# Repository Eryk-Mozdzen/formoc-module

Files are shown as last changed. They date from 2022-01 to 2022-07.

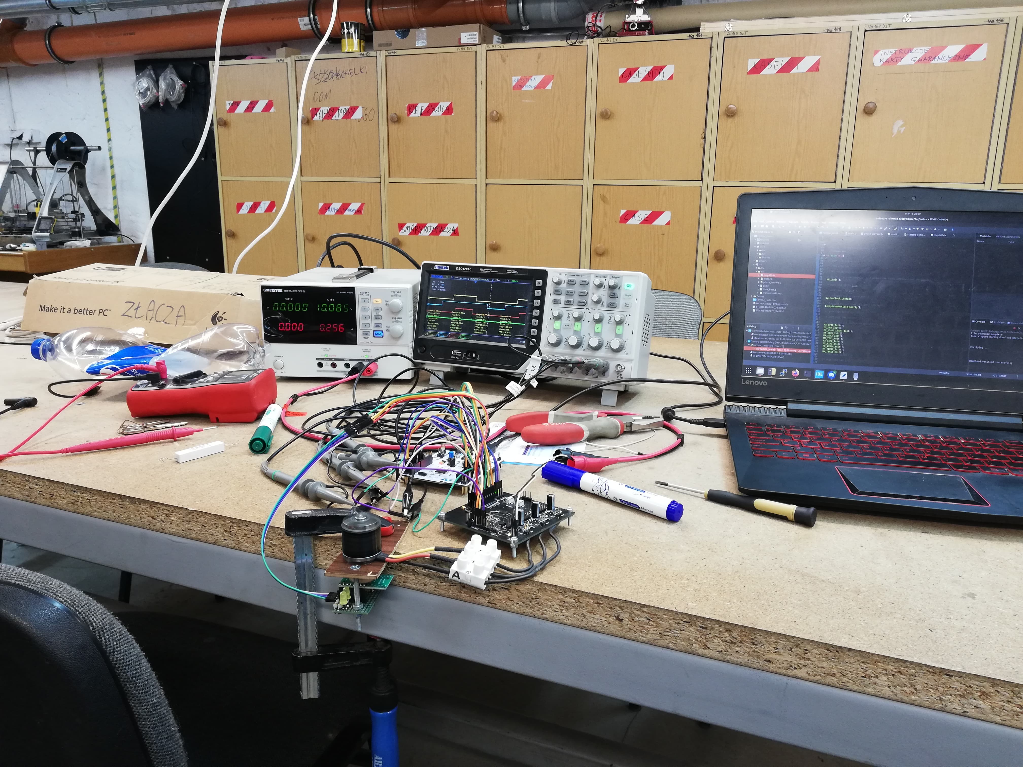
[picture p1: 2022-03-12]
docs/other_photos/275427429_1309768459516400_6027469848381933831_n.jpg

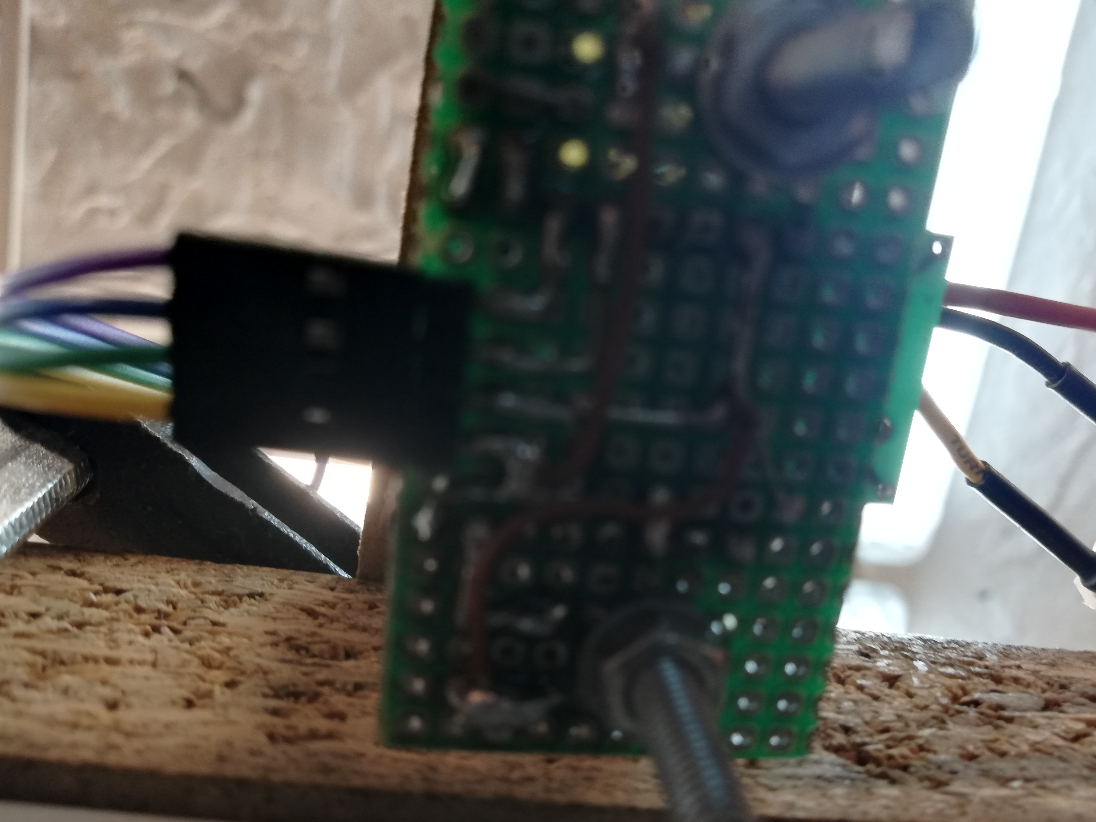
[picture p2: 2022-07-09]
docs/other_photos/IMG_20220304_194742.jpg

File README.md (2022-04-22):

# Field Oriented Motor Controller | FORMOC module
BLDC motor controller using FOC algorithm by Wojciech Bohdan and Eryk Możdżeń.

## Project overview
The goal is to create an opportunity for easy implementation of BLDC motors to small autonomous robots like linefollower or minisumo.

Right now project is in mid development stage.

## Interface

```c
struct {
  uint8_t fdc : 5;  // field code
  uint8_t tg  : 1;  // toggle
  uint8_t rw  : 1;  // read/write operation
  uint8_t mot : 1;  // left/right motor
} msg_header_tx;

struct {
  uint8_t fdc : 5;  // field code
  uint8_t tg  : 1;  // toggle
  uint8_t un  : 1;  // unused
  uint8_t mot : 1;  // left/right motor
} msg_header_rx;

struct {
  uint8_t sta : 7;  // status field
  uint8_t tg  : 1;  // toggle
} msg_hearbeat;
```

| Field | Code  | R/W | Type | Unit | Details |
| ----- | ----  | --- | ---- | ---- | --- |
| status | 0x00  | r/w | `uint8_t` | | bit 0 - MCP8024 error flag <br>bit 1 - read/write access error flag <br> bit 2 - read/write wrong toggle flag <br>  bit 3 - write timeout flag <br> bit 4 - write wrong param flag <br> bit 5-6 (unused) <br> bit 7 (reserved) |
| control (toggle free) | 0x01  | w | `uint8_t` | | bit 0 - reset <br> bit 1-7 (unused) |
|||||||
| hardware config | 0x0A  | r/w | `uint8_t` <br> `uint16_t` <br> `uint16_t` | <br> count <br> count | motor pole pairs <br> encoder CPR <br> encoder offset  |
| Id controller config | 0x0B  | r/w | `float32_t` <br> `float32_t` <br> `float32_t` ||  Kp <br> Ki <br> Kd |
| Iq controller config | 0x0C  | r/w | `float32_t` <br> `float32_t` <br> `float32_t` ||  Kp <br> Ki <br> Kd |
| velocity controller config | 0x0D  | r/w | `float32_t` <br> `float32_t` <br> `float32_t` ||  Kp <br> Ki <br> Kd |
|||||||
| velocity setpoint | 0x11 | w | `float32_t` | rps | |
|||||||
| rotor position | 0x20 | r | `int32_t` | count |
| rotor velocity | 0x21 | r | `float32_t` | rps | |
| power supply voltage  | 0x23 | r | `uint16_t` | mV | |
|||||||
| torque limit | 0x30 | w | `float32_t` | Nm | |
| velocity limit | 0x31 | w | `float32_t` | rps | |

# TODO
- check voltages
- solder cables
- one-way, reliable communication
- GET RID OF OVERCURRENT "PROTECTION"
- improve PID tunning
- find torque measurement method
- improve code organization
- add interface

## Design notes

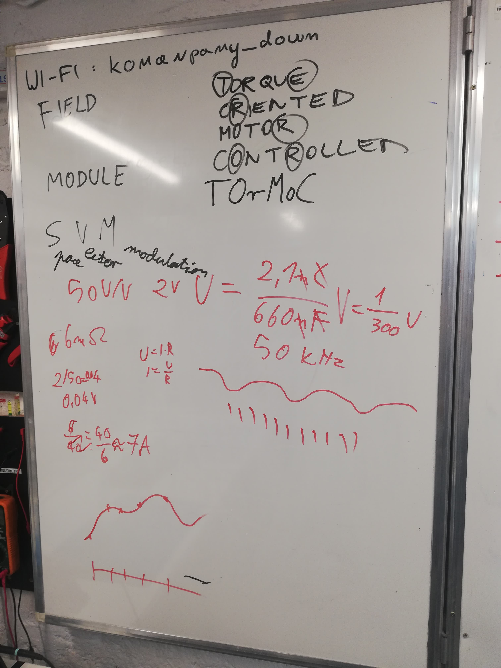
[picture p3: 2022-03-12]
docs/whiteboard_photos/275466424_334416281970746_8824751526483941625_n.jpg

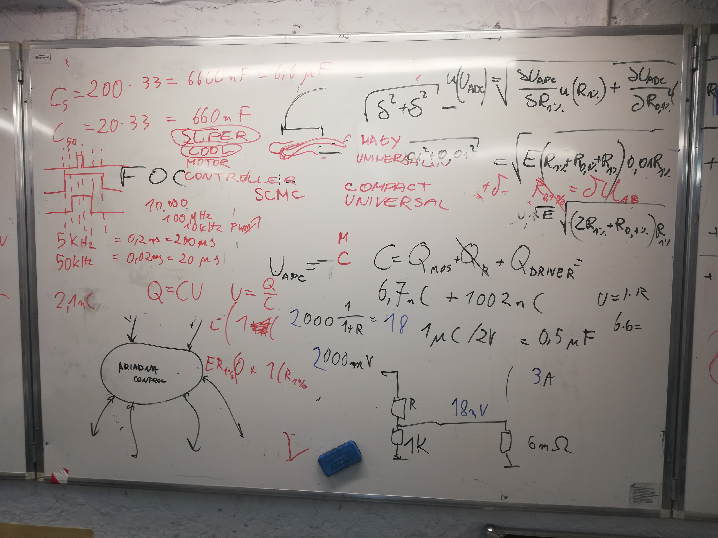
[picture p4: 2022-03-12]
docs/whiteboard_photos/275711006_301435245254634_2206148657679559166_n.jpg

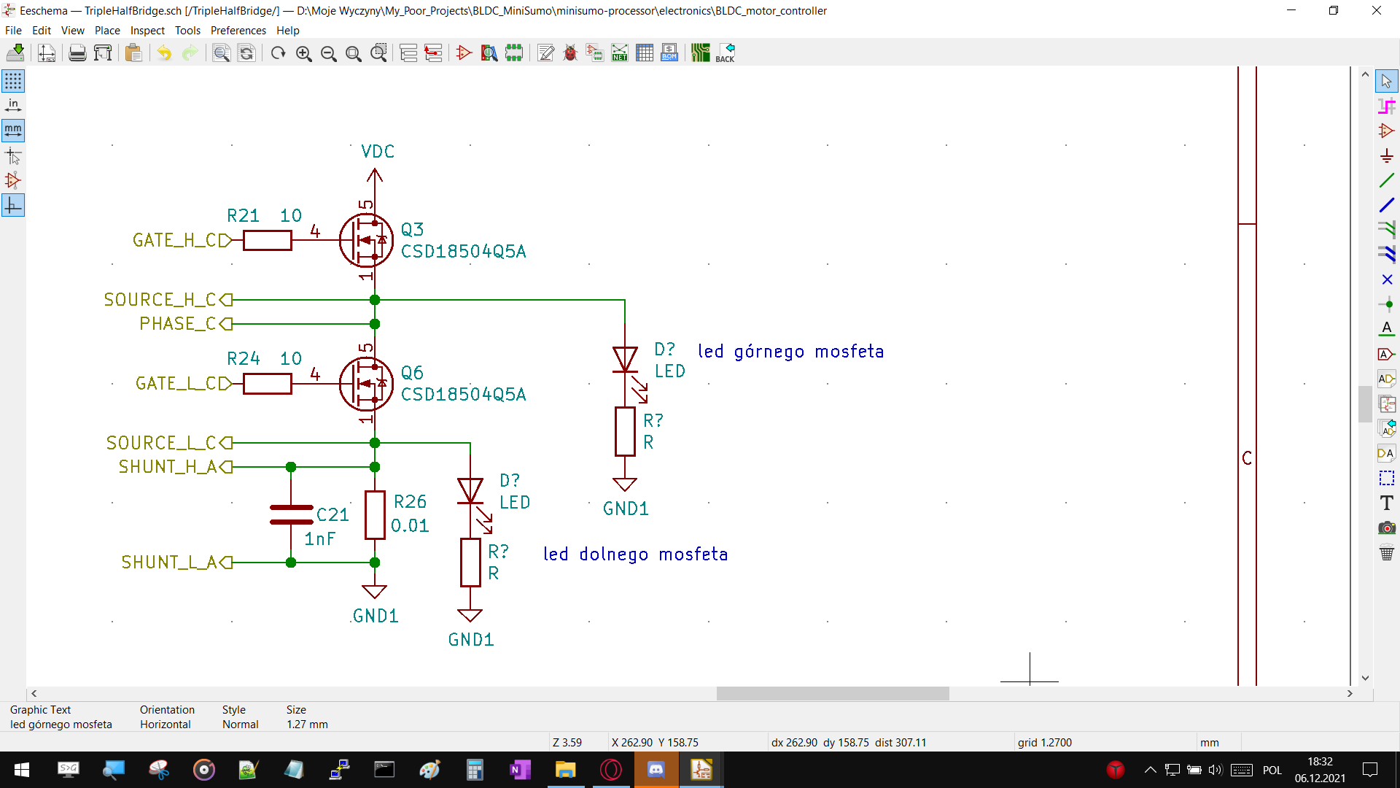
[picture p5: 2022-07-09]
docs/calculations/Screenshot (314).png

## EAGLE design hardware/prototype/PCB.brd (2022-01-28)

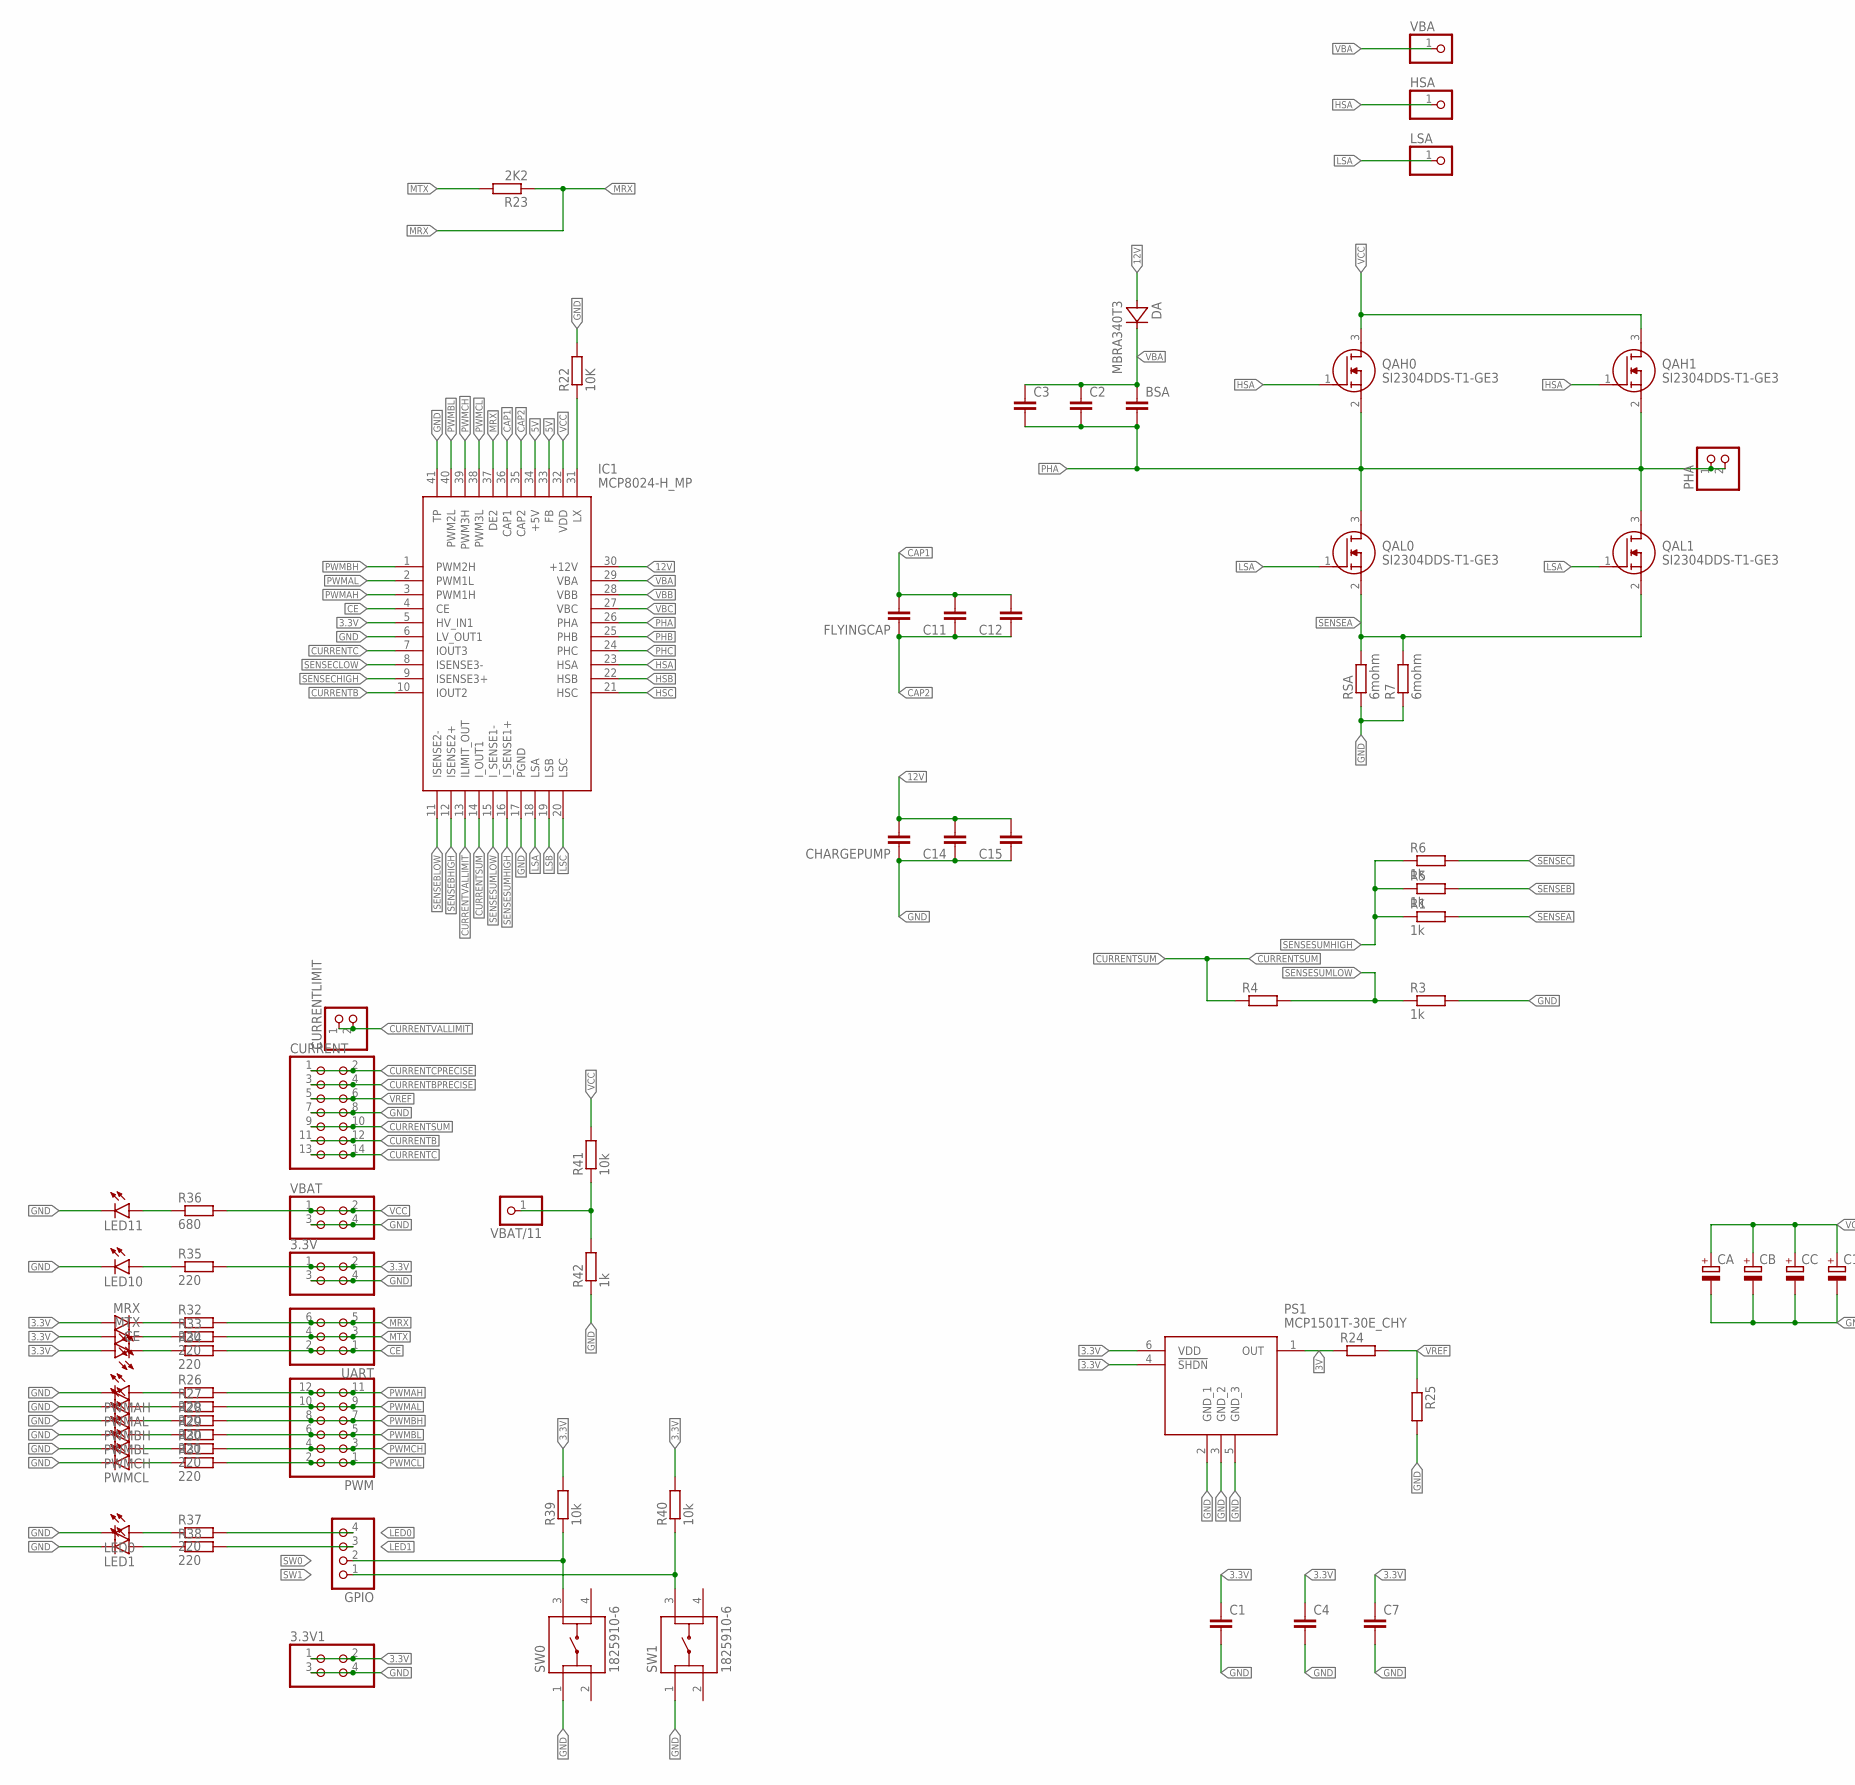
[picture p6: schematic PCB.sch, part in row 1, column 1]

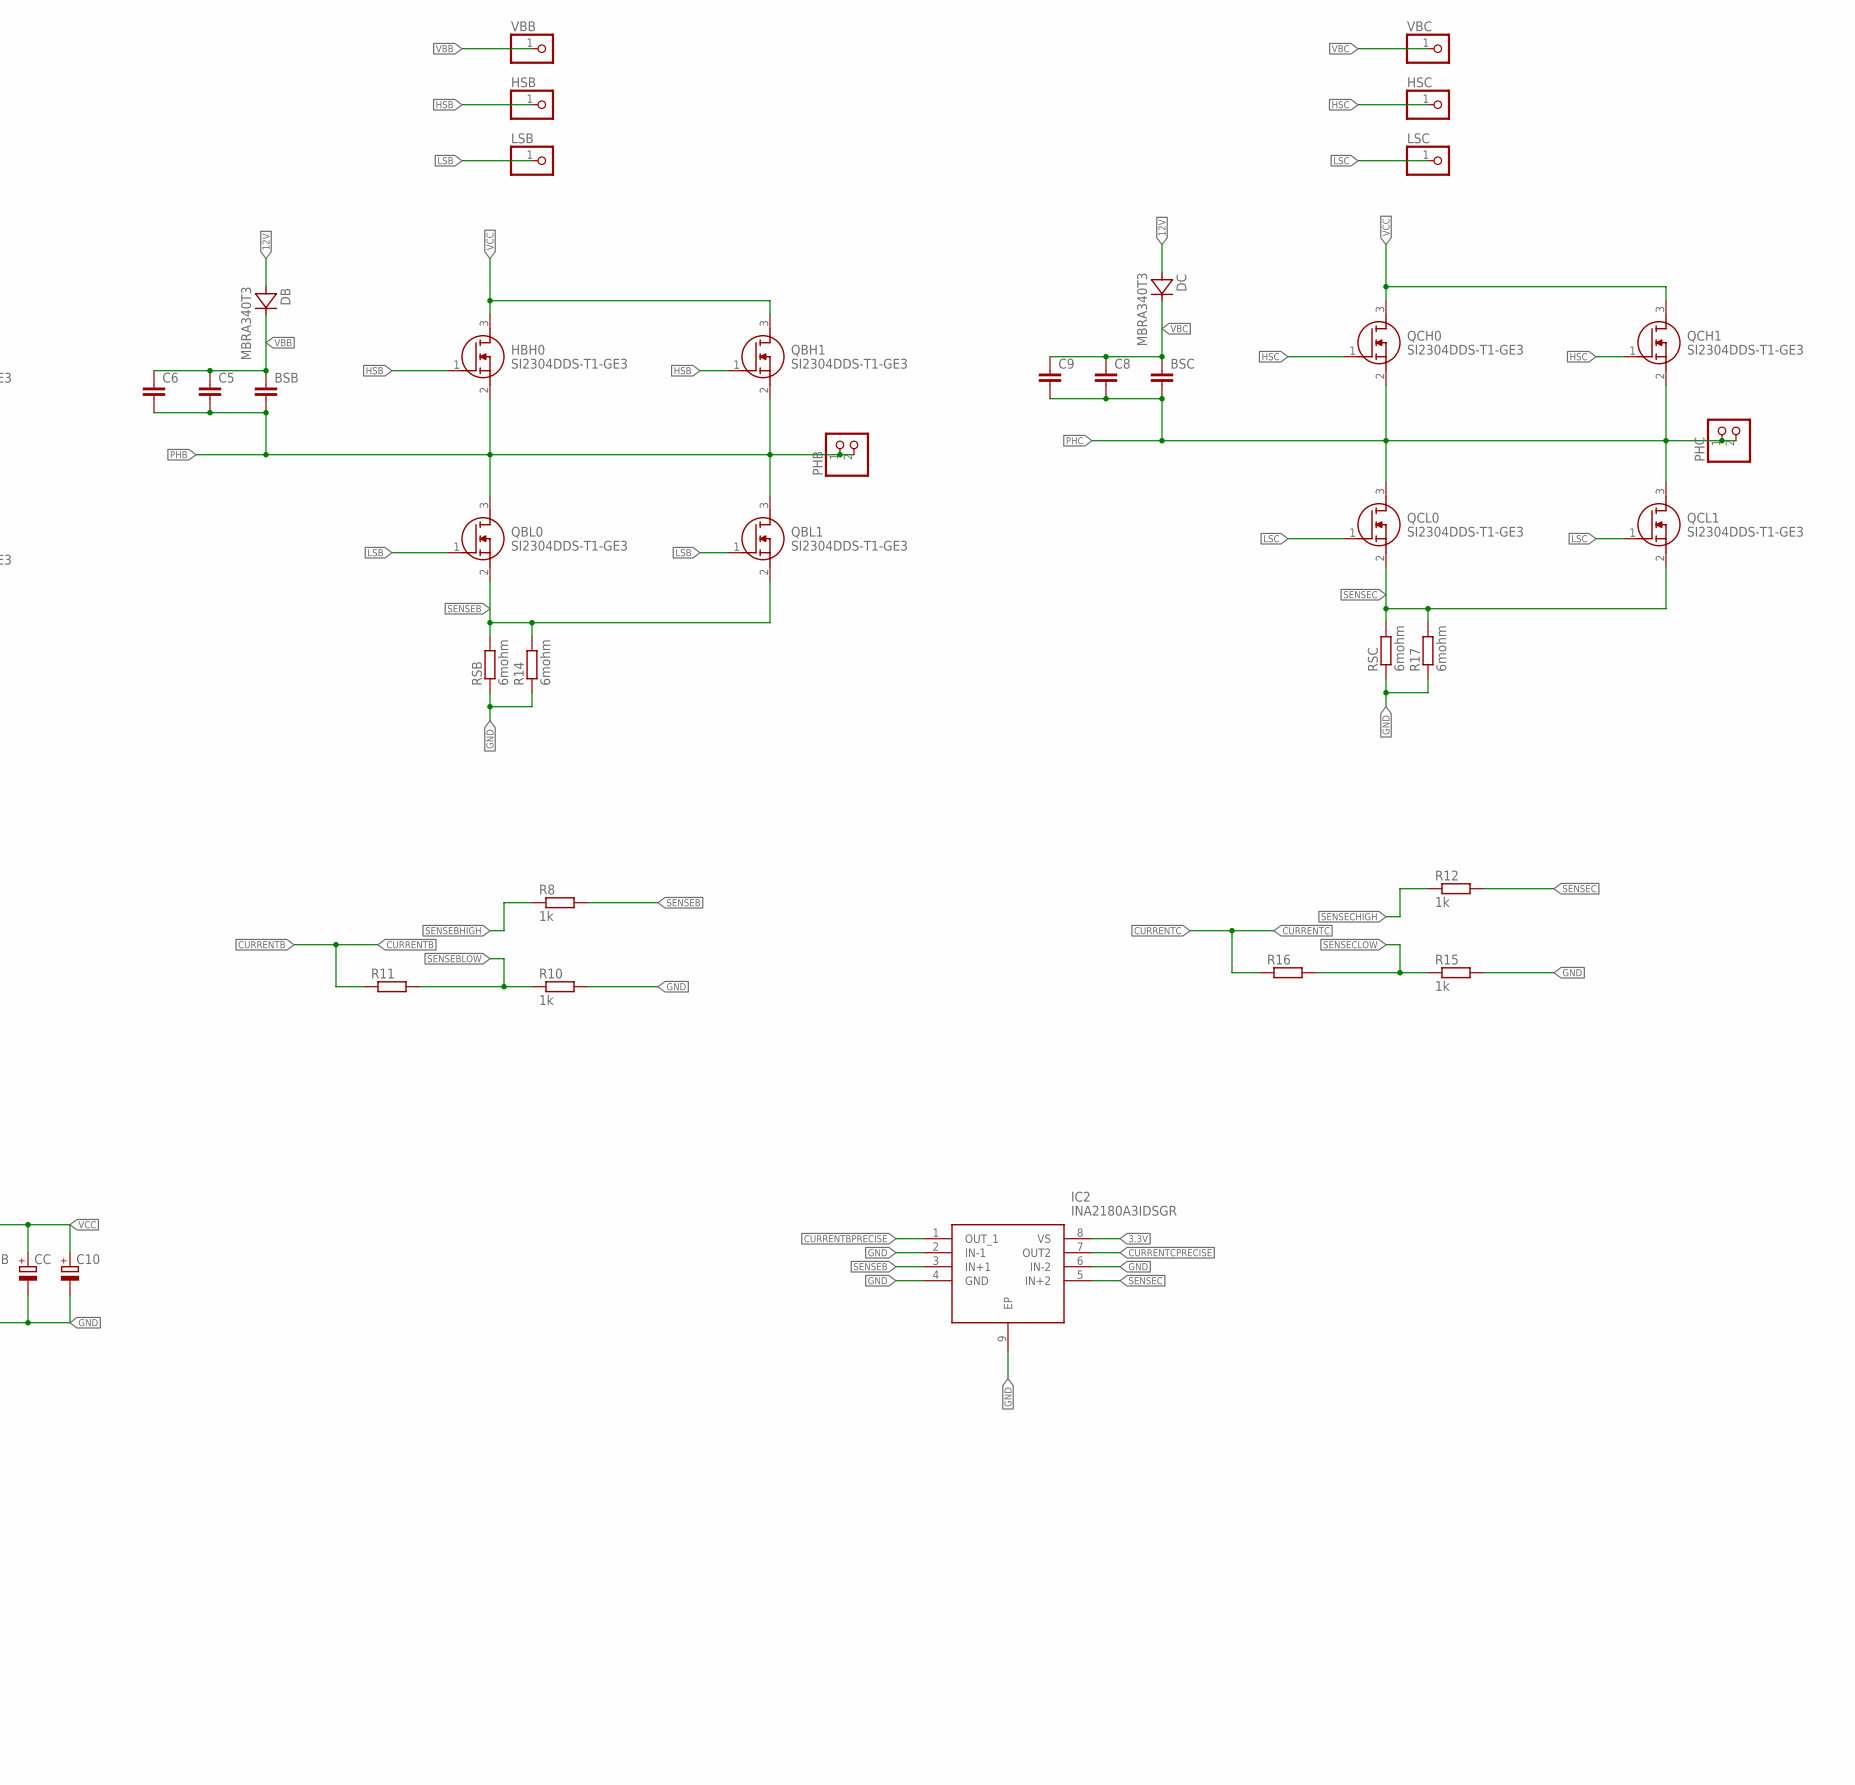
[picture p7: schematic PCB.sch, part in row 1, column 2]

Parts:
3.3V, 3.3V1: PINHD-2X2; 2X02
BSA: C-EUC0603; C0603
BSB: C-EUC0603; C0603
BSC: C-EUC0603; C0603
C1, C2, C3, C4, C5, C6, C7, C8, C9, C11, C12, C14, C15: C-EUC0603; C0603
C10: CPOL-EUE3.5-8; E3,5-8
CA: CPOL-EUE3.5-8; E3,5-8
CB: CPOL-EUE3.5-8; E3,5-8
CC: CPOL-EUE3.5-8; E3,5-8
CE: LEDCHIPLED_0805; CHIPLED_0805
CHARGEPUMP: C-EUC0603; C0603
CURRENT: PINHD-2X7; 2X07
CURRENTLIMIT: PINHD-1X2; 1X02
DA: MBRA340T3; SMA
DB: MBRA340T3; SMA
DC: MBRA340T3; SMA
FLYINGCAP: C-EUC0603; C0603
GPIO: PINHD-1X4; 1X04
HBH0: SI2304DDS-T1-GE3; SOT95P237X112-3N
HSA: PINHD-1X1; 1X01
HSB: PINHD-1X1; 1X01
HSC: PINHD-1X1; 1X01
IC1: MCP8024-H_MP; QFN40P500X500X90-41N
IC2: INA2180A3IDSGR; SON50P200X200X80-9N
LED0, LED1, LED10, LED11: LEDCHIPLED_0805; CHIPLED_0805
LSA: PINHD-1X1; 1X01
LSB: PINHD-1X1; 1X01
LSC: PINHD-1X1; 1X01
MRX: LEDCHIPLED_0805; CHIPLED_0805
MTX: LEDCHIPLED_0805; CHIPLED_0805
PHA: PINHD-1X2; 1X02
PHB: PINHD-1X2; 1X02
PHC: PINHD-1X2; 1X02
PS1: MCP1501T-30E_CHY; SOT95P270X145-6N
PWM: PINHD-2X6; 2X06
PWMAH: LEDCHIPLED_0805; CHIPLED_0805
PWMAL: LEDCHIPLED_0805; CHIPLED_0805
PWMBH: LEDCHIPLED_0805; CHIPLED_0805
PWMBL: LEDCHIPLED_0805; CHIPLED_0805
PWMCH: LEDCHIPLED_0805; CHIPLED_0805
PWMCL: LEDCHIPLED_0805; CHIPLED_0805
QAH0, QAH1: SI2304DDS-T1-GE3; SOT95P237X112-3N
QAL0, QAL1: SI2304DDS-T1-GE3; SOT95P237X112-3N
QBH1: SI2304DDS-T1-GE3; SOT95P237X112-3N
QBL0, QBL1: SI2304DDS-T1-GE3; SOT95P237X112-3N
QCH0, QCH1: SI2304DDS-T1-GE3; SOT95P237X112-3N
QCL0, QCL1: SI2304DDS-T1-GE3; SOT95P237X112-3N
R1, R3, R5, R6, R8, R10, R12, R15, R42: 1k; R0805
R4, R11, R16, R24, R25: R-EU_R0805; R0805
R7, R14, R17: 6mohm; R1206
R22: 10K; R0805
R23: 2K2; R0805
R26, R27, R28, R29, R30, R31, R32, R33, R34, R35, R37, R38: 220; R0805
R36: 680; R0805
R39, R40, R41: 10k; R0805
RSA: 6mohm; R1206
RSB: 6mohm; R1206
RSC: 6mohm; R1206
SW0, SW1: 1825910-6
UART: PINHD-2X3; 2X03
VBA: PINHD-1X1; 1X01
VBAT: PINHD-2X2; 2X02
VBAT/11: PINHD-1X1; 1X01
VBB: PINHD-1X1; 1X01
VBC: PINHD-1X1; 1X01

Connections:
3.3V: 3.3V.1, 3.3V.2, 3.3V1.1, 3.3V1.2, C1.1, C4.1, C7.1, CE.A, IC1.5 (HV_IN1), IC2.8 (VS), MRX.A, MTX.A, PS1.4 (!SHDN), PS1.6 (VDD), R35.2, R39.2, R40.2
3V: PS1.1 (OUT), R24.1
5V: IC1.33 (FB), IC1.34 (+5V)
12V: C14.2, C15.2, CHARGEPUMP.2, DA.A, DB.A, DC.A, IC1.30 (+12V)
CAP1: C11.2, C12.2, FLYINGCAP.2, IC1.36 (CAP1)
CAP2: C11.1, C12.1, FLYINGCAP.1, IC1.35 (CAP2)
CE: IC1.4 (CE), R34.2, UART.1, UART.2
CURRENTB: CURRENT.11, CURRENT.12, IC1.10 (IOUT2), R11.1
CURRENTBPRECISE: CURRENT.3, CURRENT.4, IC2.1 (OUT_1)
CURRENTC: CURRENT.13, CURRENT.14, IC1.7 (IOUT3), R16.1
CURRENTCPRECISE: CURRENT.1, CURRENT.2, IC2.7 (OUT2)
CURRENTSUM: CURRENT.9, CURRENT.10, IC1.14 (I_OUT1), R4.1
CURRENTVALLIMIT: CURRENTLIMIT.1, CURRENTLIMIT.2, IC1.13 (ILIMIT_OUT)
GND: 3.3V.3, 3.3V.4, 3.3V1.3, 3.3V1.4, C1.2, C4.2, C7.2, C10.-, C14.1, C15.1, CA.-, CB.-, CC.-, CHARGEPUMP.1, CURRENT.7, CURRENT.8, IC1.6 (LV_OUT1), IC1.17 (PGND), IC1.41 (TP), IC2.2 (IN-1), IC2.4 (GND), IC2.6 (IN-2), IC2.9 (EP), LED0.C, LED1.C, LED10.C, LED11.C, PS1.2 (GND_1), PS1.3 (GND_2), PS1.5 (GND_3), PWMAH.C, PWMAL.C, PWMBH.C, PWMBL.C, PWMCH.C, PWMCL.C, R3.2, R7.1, R10.2, R14.1, R15.2, R17.1, R22.2, R25.2, R42.1, RSA.1, RSB.1, RSC.1, SW0.1, SW1.1, VBAT.3, VBAT.4
HSA: HSA.1, IC1.23 (HSA), QAH0.1 (G), QAH1.1 (G)
HSB: HBH0.1 (G), HSB.1, IC1.22 (HSB), QBH1.1 (G)
HSC: HSC.1, IC1.21 (HSC), QCH0.1 (G), QCH1.1 (G)
LED0: GPIO.4, R37.2
LED1: GPIO.3, R38.2
LSA: IC1.18 (LSA), LSA.1, QAL0.1 (G), QAL1.1 (G)
LSB: IC1.19 (LSB), LSB.1, QBL0.1 (G), QBL1.1 (G)
LSC: IC1.20 (LSC), LSC.1, QCL0.1 (G), QCL1.1 (G)
MRX: IC1.37 (DE2), R23.1, R32.2, UART.5, UART.6
MTX: R23.2, R33.2, UART.3, UART.4
unnamed: IC1.31 (LX), R22.1
unnamed: PWMAH.A, R26.1
unnamed: PWMAL.A, R27.1
unnamed: PWMBH.A, R28.1
unnamed: PWMBL.A, R29.1
unnamed: PWMCH.A, R30.1
unnamed: PWMCL.A, R31.1
unnamed: MRX.C, R32.1
unnamed: MTX.C, R33.1
unnamed: CE.C, R34.1
unnamed: LED10.A, R35.1
unnamed: LED11.A, R36.1
unnamed: LED0.A, R37.1
unnamed: LED1.A, R38.1
unnamed: R41.1, R42.2, VBAT/11.1
PHA: BSA.2, C2.2, C3.2, IC1.26 (PHA), PHA.1, PHA.2, QAH0.2 (S), QAH1.2 (S), QAL0.3 (D), QAL1.3 (D)
PHB: BSB.2, C5.2, C6.2, HBH0.2 (S), IC1.25 (PHB), PHB.1, PHB.2, QBH1.2 (S), QBL0.3 (D), QBL1.3 (D)
PHC: BSC.2, C8.2, C9.2, IC1.24 (PHC), PHC.1, PHC.2, QCH0.2 (S), QCH1.2 (S), QCL0.3 (D), QCL1.3 (D)
PWMAH: IC1.3 (PWM1H), PWM.11, PWM.12, R26.2
PWMAL: IC1.2 (PWM1L), PWM.9, PWM.10, R27.2
PWMBH: IC1.1 (PWM2H), PWM.7, PWM.8, R28.2
PWMBL: IC1.40 (PWM2L), PWM.5, PWM.6, R29.2
PWMCH: IC1.39 (PWM3H), PWM.3, PWM.4, R30.2
PWMCL: IC1.38 (PWM3L), PWM.1, PWM.2, R31.2
SENSEA: QAL0.2 (S), QAL1.2 (S), R1.2, R7.2, RSA.2
SENSEB: IC2.3 (IN+1), QBL0.2 (S), QBL1.2 (S), R5.2, R8.2, R14.2, RSB.2
SENSEBHIGH: IC1.12 (ISENSE2+), R8.1
SENSEBLOW: IC1.11 (ISENSE2-), R10.1, R11.2
SENSEC: IC2.5 (IN+2), QCL0.2 (S), QCL1.2 (S), R6.2, R12.2, R17.2, RSC.2
SENSECHIGH: IC1.9 (ISENSE3+), R12.1
SENSECLOW: IC1.8 (ISENSE3-), R15.1, R16.2
SENSESUMHIGH: IC1.16 (I_SENSE1+), R1.1, R5.1, R6.1
SENSESUMLOW: IC1.15 (I_SENSE1-), R3.1, R4.2
SW0: GPIO.2, R39.1, SW0.3
SW1: GPIO.1, R40.1, SW1.3
VBA: BSA.1, C2.1, C3.1, DA.C, IC1.29 (VBA), VBA.1
VBB: BSB.1, C5.1, C6.1, DB.C, IC1.28 (VBB), VBB.1
VBC: BSC.1, C8.1, C9.1, DC.C, IC1.27 (VBC), VBC.1
VCC: C10.+, CA.+, CB.+, CC.+, HBH0.3 (D), IC1.32 (VDD), QAH0.3 (D), QAH1.3 (D), QBH1.3 (D), QCH0.3 (D), QCH1.3 (D), R36.2, R41.2, VBAT.1, VBAT.2
VREF: CURRENT.5, CURRENT.6, R24.2, R25.1

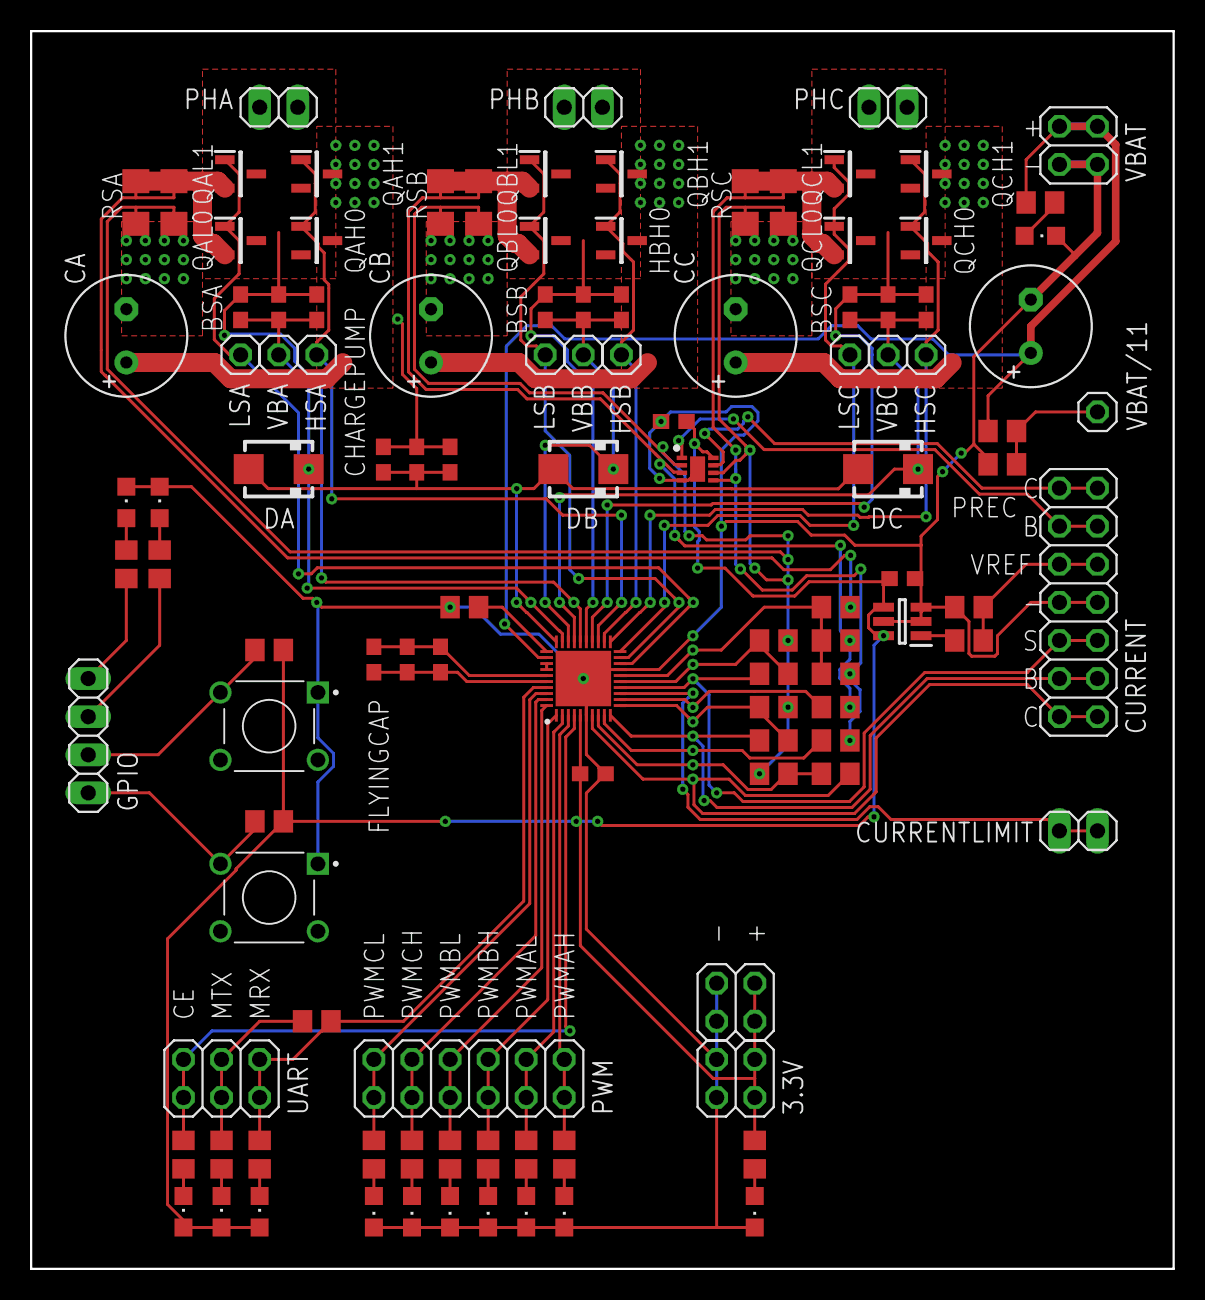
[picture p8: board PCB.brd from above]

Board: 2 copper layers, 76.2 x 82.5 mm, 114 parts (0 on the bottom side), 64 nets.

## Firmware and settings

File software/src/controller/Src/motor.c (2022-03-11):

#include "motor.h"

void Motor_Init(Motor_t *motor, TIM_HandleTypeDef *encoder_timer, float mechanical_offset) {
	motor->encoder_timer = encoder_timer;
	motor->mechanical_offset = mechanical_offset;

	HAL_TIM_Encoder_Start(motor->encoder_timer, TIM_CHANNEL_1);
	HAL_TIM_Encoder_Start(motor->encoder_timer, TIM_CHANNEL_2);

	__HAL_TIM_SET_COUNTER(motor->encoder_timer, 0);
}

float Motor_GetMechanicalPosition(Motor_t *motor) {
	float encoder = __HAL_TIM_GET_COUNTER(motor->encoder_timer);
	motor->mechanical_pos = encoder/MOTOR_ENCODER_CPR;

	return fmodf(motor->mechanical_pos + motor->mechanical_offset, 1.f);
}

float Motor_GetElectricalPosition(Motor_t *motor) {
	float elec = Motor_GetMechanicalPosition(motor)*MOTOR_POLE_PAIRS;

	motor->electrical_pos = fmodf(elec, 1.f);

	return motor->electrical_pos;
}

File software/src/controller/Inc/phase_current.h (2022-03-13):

#ifndef INC_PHASE_CURRENT_H_
#define INC_PHASE_CURRENT_H_

#include "stm32l4xx_hal.h"
#include "utilities.h"
#include <math.h>

#define PHASE_CURRENT_ADC_RESOLUTION	4095	// LSB
#define PHASE_CURRENT_ADC_REFERENCE		3.3f	// V
#define PHASE_CURRENT_GET_ADC_VOLTAGE(lsb)		(((lsb)*PHASE_CURRENT_ADC_REFERENCE)/PHASE_CURRENT_ADC_RESOLUTION)	// V

#define PHASE_CURRENT_A_CONST					(0.623f/(0.951f - 0.89f))
#define PHASE_CURRENT_B_CONST					(-PHASE_CURRENT_A_CONST*0.89f)
#define PHASE_CURRENT_VOLT_TO_AMP(vol)			(PHASE_CURRENT_A_CONST*(vol) + PHASE_CURRENT_B_CONST)

typedef struct {
	ADC_HandleTypeDef *b_phase_adc;
	ADC_HandleTypeDef *c_phase_adc;

	uint16_t phase_buffer[2];

	uint8_t ready;

	float32x3_t voltage;
	float32x3_t current;

	float32x3_t peak_voltage;
	float32x3_t peak_current;
} PhaseCurrent_t;

void PhaseCurrent_Init(PhaseCurrent_t *, ADC_HandleTypeDef *, ADC_HandleTypeDef *);
void PhaseCurrent_Reset(PhaseCurrent_t *);

void PhaseCurrent_ConvCpltCallback(PhaseCurrent_t *, ADC_HandleTypeDef *);

uint8_t PhaseCurrent_IsReady(PhaseCurrent_t *);
float32x3_t PhaseCurrent_GetCurrent(PhaseCurrent_t *);

#endif

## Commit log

2022-01-28 Add prototype hardware
    [PCB.brd, PCB.sch]
2022-01-29 Add caps.txt in prototype
2022-01-29 Add linefollower motors calculations
    [motor parametrs.xlsx]
2022-02-08 phase current sense
2022-02-08 rotor position utilities
2022-02-11 communication through DMA
2022-03-05 current sensing tests
2022-03-05 correct interrupt for current sense
    [formoc_test01.ioc, main.c, mcp8024.c]
2022-03-05 current sensing preparation
2022-03-11 DMA ADC conversion in right moment
2022-03-11 PIDs constants and encoder offset
2022-03-11 PID tunning
